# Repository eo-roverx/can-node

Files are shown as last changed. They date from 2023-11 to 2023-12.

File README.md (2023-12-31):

# CAN Node PCB Designs

Part of the new arm system, wherein each PCB drives one motor, provides it feedback control, and (if needed) gives back IMU and encoder data. Our CAN node will have the following features:

- CAN bus communication
- IMU (accelerometer, gyroscope)
- Motor encoder input
- Motor driver
- 4 user defined LEDs + one status LED
- 4 bit address DIP switch
- ESP32 microcontroller: integration and feedback control

## Components
- ESP32 Microcontroller
- ESP32 power capacitor
- MPU9250 IMU
- MCP2551 CAN Transceiver
- 2x CAN RJ45 ports
- 2x XT60 solder pads for power
- MD13 Motor Driver
- MD13 power XT60 solder pads
- MD13 signal JST
- motor encoder JST
- 5V buck converter
- 2x 4.7k ohms I2C pull-up resistors
- CAN termination resistor solder pads
- I2C debug solder pads
- CAN Rx-Tx debug solder pads
- 4x dip switch
- 4x 10k ohm pull-down resistors
- 1 power LED
- 1 status LED
- 4 user defined LEDs
    - 2 used for CRx-CTx
    - 1 used for MPU calibration
    - 1 used for sync
- 6x 2k ohm current limiting resistors

## ESP32 Pin-out

ESP32 Pin-out

### CAN Bus
-  D2 CAN Rx
- D15 CAN Tx

### IMU
- D21 SDA
- D22 SCL
- D18 FSYNC
- D19 INT

### Motor encoder
- D34 pin A
- D33 pin B

### MD13 Motor Driver
- D26 PWM
- D25 DIR

### LEDs
- D32 status
- D13 user 0 (Sync: all nodes are connected)
- D12 user 1 (CAN Rx)
- D14 user 2 (CAN Tx)
- D27 user 3 (MPU calibration)

### Address DIP switches
- D4 address 0
- RX2 address 1
- TX2 address 2
- D5 address 3

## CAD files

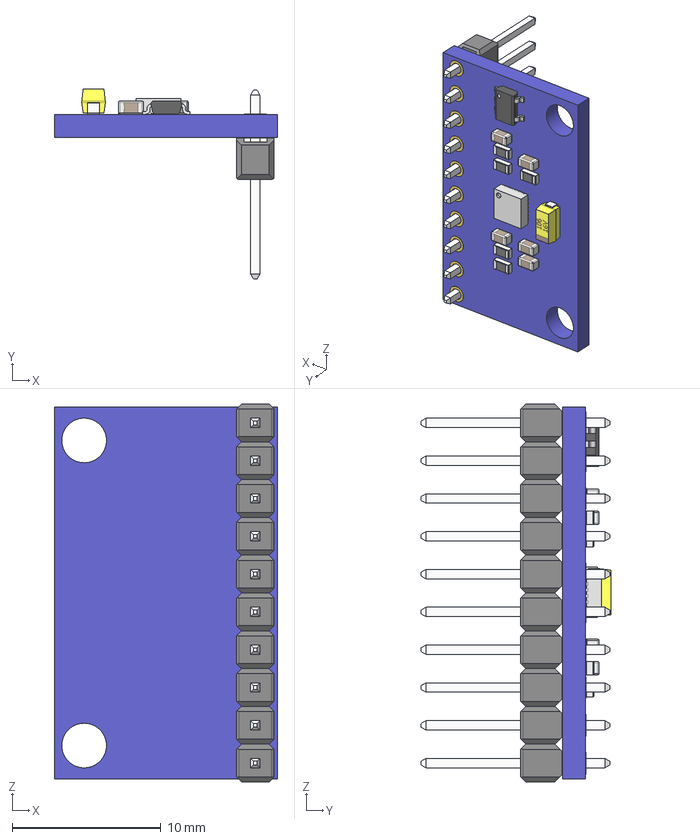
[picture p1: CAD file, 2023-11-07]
custom-libs/3d/MPU-9250.stp
15.0 x 12.8 x 25.4 mm
board
hole_plating x 20
Pin Header 1x10 TH Pitch 2.54mm
MPU-9250_1
tantalum 10uF
SOT23_5
RESC-0603 x 5
CAPC-0603-T0.9-BN x 5

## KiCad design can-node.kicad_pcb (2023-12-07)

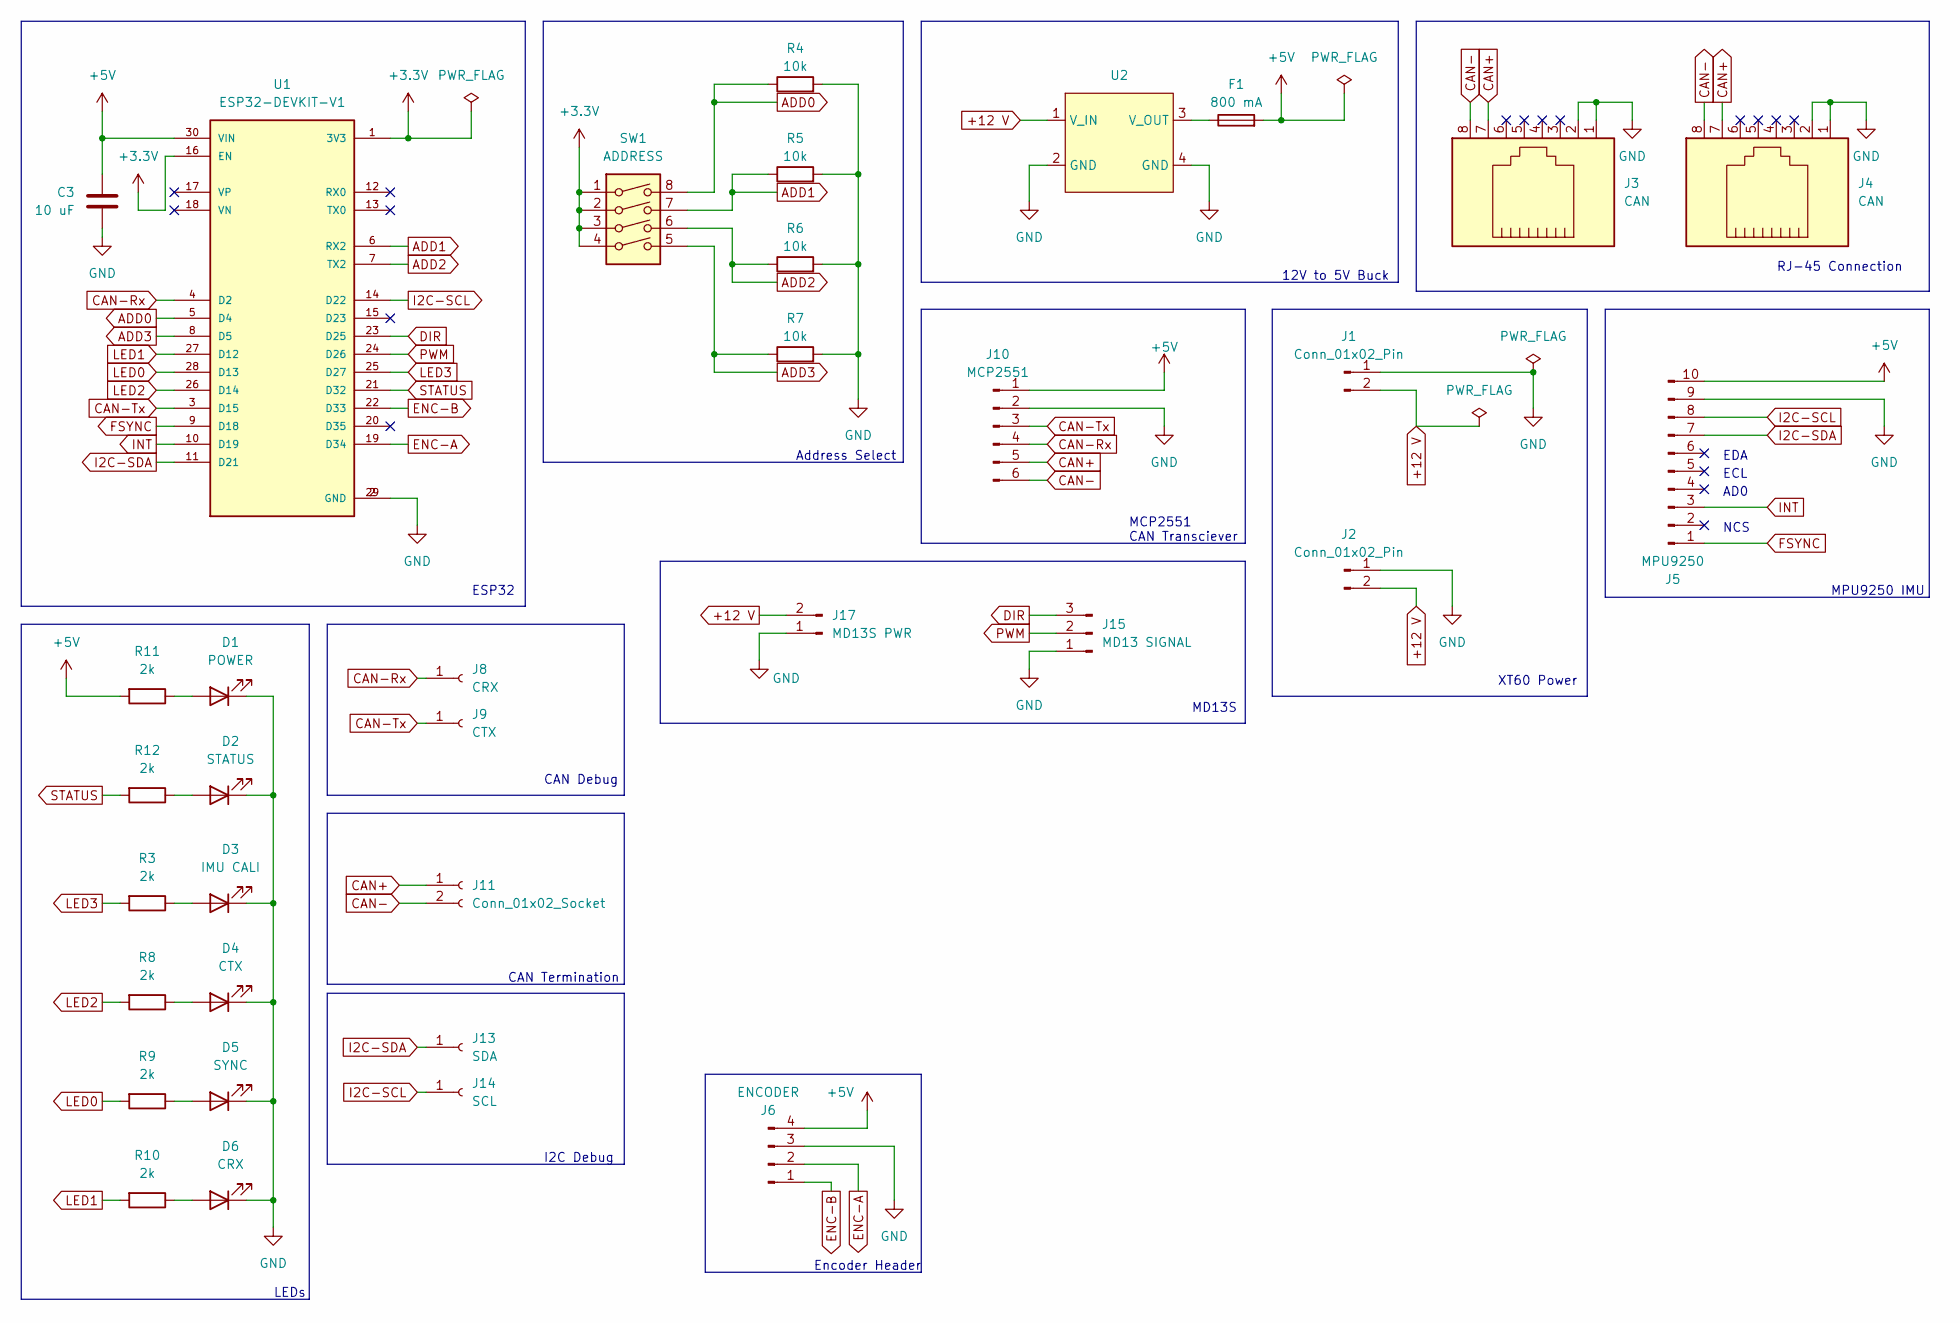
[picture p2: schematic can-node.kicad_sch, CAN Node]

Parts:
C3: 10 uF; C_0805_2012Metric
D1: POWER; LED_D3.0mm
D2: STATUS; LED_D3.0mm
D3: IMU CALI; LED_D3.0mm
D4: CTX; LED_D3.0mm
D5: SYNC; LED_D3.0mm
D6: CRX; LED_D3.0mm
F1: 800 mA; Fuse_0805_2012Metric_Pad1.15x1.40mm_HandSolder
J1, J2: Conn_01x02_Pin; SolderWire-1.5sqmm_1x02_P7.8mm_D1.7mm_OD3.9mm
J3, J4: CAN; RJ45_Amphenol_54602-x08_Horizontal
J5: MPU9250; PinHeader_1x10_P2.54mm_Vertical
J6: ENCODER; JST_PH_B4B-PH-K_1x04_P2.00mm_Vertical
J8: CRX; SolderWire-0.1sqmm_1x01_D0.4mm_OD1mm
J9: CTX; SolderWire-0.1sqmm_1x01_D0.4mm_OD1mm
J10: MCP2551; PinHeader_1x06_P2.54mm_Vertical
J11: Conn_01x02_Socket; SolderWire-0.1sqmm_1x02_P3.6mm_D0.4mm_OD1mm
J13: SDA; SolderWire-0.1sqmm_1x01_D0.4mm_OD1mm
J14: SCL; SolderWire-0.1sqmm_1x01_D0.4mm_OD1mm
J15: MD13 SIGNAL; JST_PH_S3B-PH-K_1x03_P2.00mm_Horizontal
J17: MD13S PWR; SolderWire-1sqmm_1x02_P7.8mm_D1.4mm_OD3.9mm
R3, R8, R9, R10, R11, R12: 2k; R_Axial_DIN0204_L3.6mm_D1.6mm_P5.08mm_Horizontal
R4, R5, R6, R7: 10k; R_Axial_DIN0204_L3.6mm_D1.6mm_P5.08mm_Horizontal
SW1: ADDRESS; SW_DIP_SPSTx04_Slide_6.7x11.72mm_W7.62mm_P2.54mm_LowProfile
U1: ESP32-DEVKIT-V1; MODULE_ESP32_DEVKIT_V1; PARTREV N/A
U2: MINI_360_Buck

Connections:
+3.3V: SW1.1, SW1.2, SW1.3, SW1.4, U1.1 (3V3), U1.16 (EN)
+5V: C3.1, F1.2, J5.10, J6.4, J10.1, R11.2, U1.30 (VIN)
+12 V: J1.2, J2.2, J17.2, U2.1 (V_IN)
ADD0: R4.1, SW1.8, U1.5 (D4)
ADD1: R5.1, SW1.7, U1.6 (RX2)
ADD2: R6.1, SW1.6, U1.7 (TX2)
ADD3: R7.1, SW1.5, U1.8 (D5)
CAN+: J3.7, J4.7, J10.5, J11.1
CAN-: J3.8, J4.8, J10.6, J11.2
CAN-Rx: J8.1, J10.4, U1.4 (D2)
CAN-Tx: J9.1, J10.3, U1.3 (D15)
DIR: J15.3, U1.23 (D25)
ENC-A: J6.2, U1.19 (D34)
ENC-B: J6.1, U1.22 (D33)
FSYNC: J5.1, U1.9 (D18)
GND: C3.2, D1.1 (K), D2.1 (K), D3.1 (K), D4.1 (K), D5.1 (K), D6.1 (K), J1.1, J2.1, J3.1, J3.2, J4.1, J4.2, J5.9, J6.3, J10.2, J15.1, J17.1, R4.2, R5.2, R6.2, R7.2, U1.2 (GND), U1.29 (GND), U2.2 (GND), U2.4 (GND)
I2C-SCL: J5.8, J14.1, U1.14 (D22)
I2C-SDA: J5.7, J13.1, U1.11 (D21)
INT: J5.3, U1.10 (D19)
LED0: R9.2, U1.28 (D13)
LED1: R10.2, U1.27 (D12)
LED2: R8.2, U1.26 (D14)
LED3: R3.2, U1.25 (D27)
unnamed: D1.2 (A), R11.1
unnamed: D2.2 (A), R12.1
unnamed: D3.2 (A), R3.1
unnamed: D4.2 (A), R8.1
unnamed: D5.2 (A), R9.1
unnamed: D6.2 (A), R10.1
unnamed: F1.1, U2.3 (V_OUT)
PWM: J15.2, U1.24 (D26)
STATUS: R12.2, U1.21 (D32)

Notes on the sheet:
ESP32
12V to 5V Buck
NCS
RJ-45 Connection
Address Select
MCP2551 CAN Transciever
CAN Termination
I2C Debug
ECL
XT60 Power
MPU9250 IMU
MD13S
LEDs
Encoder Header
AD0
CAN Debug
EDA

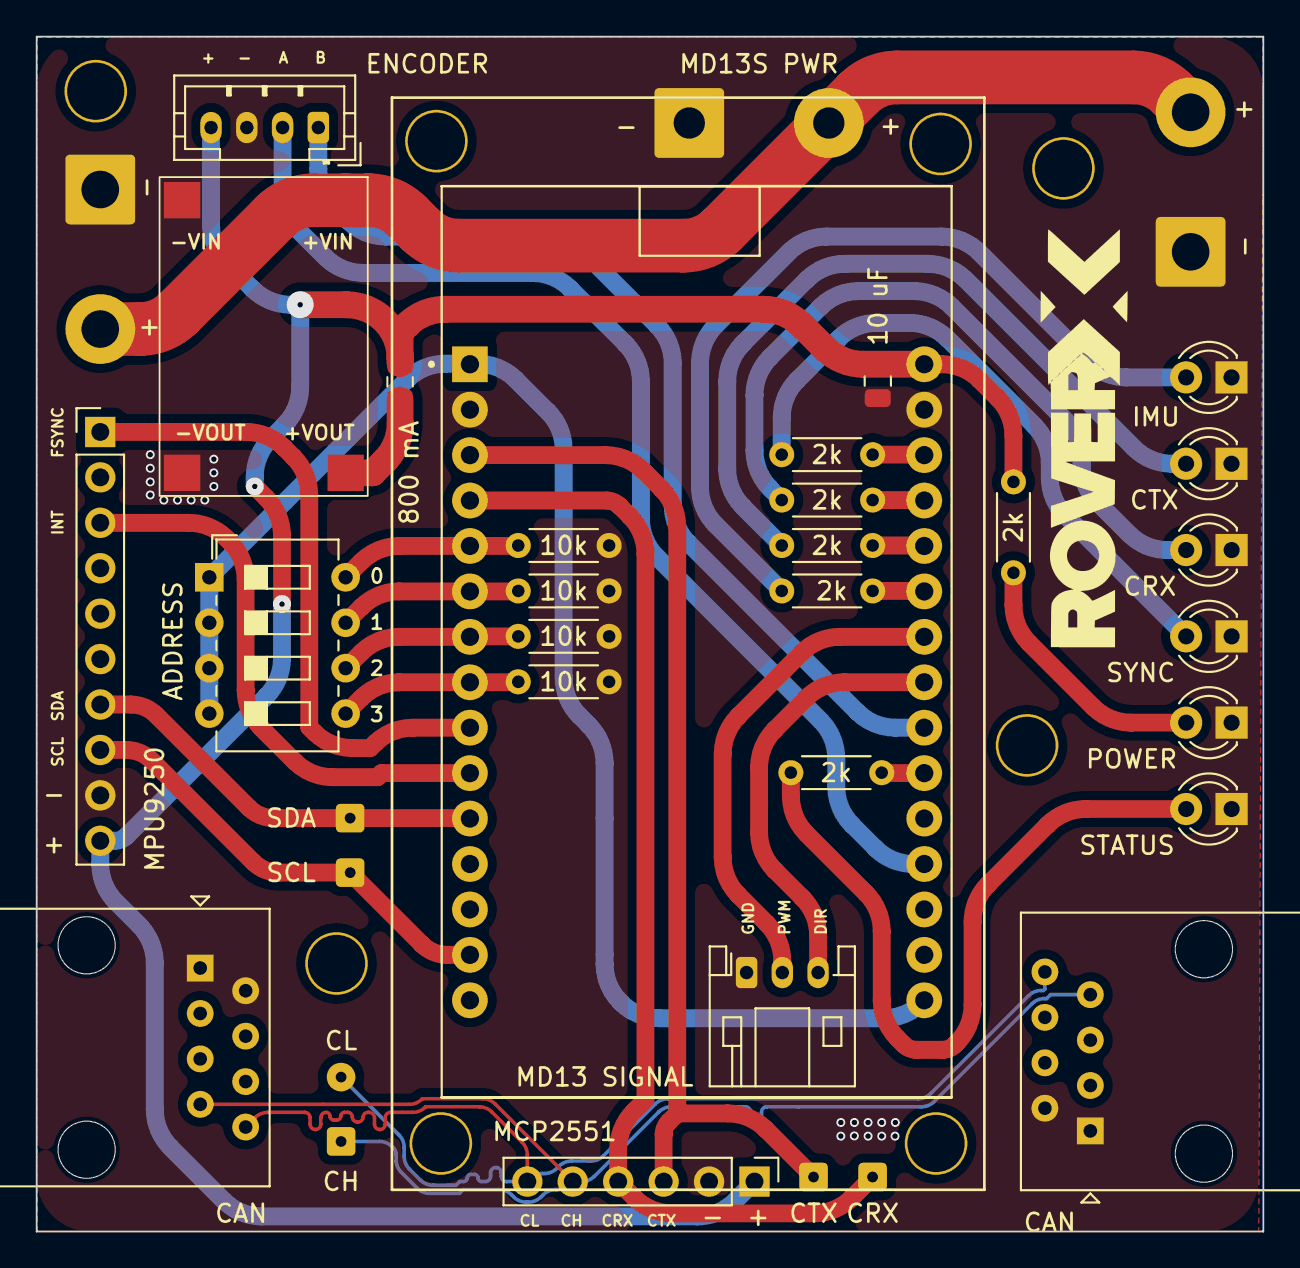
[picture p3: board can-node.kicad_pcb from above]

Board: 2 copper layers, 68.6 x 66.8 mm, 35 parts (0 on the bottom side), 32 nets.

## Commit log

2023-11-03 v1 for esp32 breakout
    [can-node.kicad_pcb, can-node.kicad_sch]
2023-11-04 placed PCB components
    [can-node.kicad_pcb, can-node.kicad_sch]
2023-11-04 additional labelling
    [can-node.kicad_pcb]
2023-11-06 first try
    [can-node.kicad_pcb, can-node.kicad_sch]
2023-11-07 fixed footprints
    [can-node.kicad_pcb, can-node.kicad_sch]
2023-11-07 routing attempt
    [can-node.kicad_pcb, can-node.kicad_sch]
2023-11-07 update for 3D
    [can-node.kicad_pcb, can-node.kicad_sch]
2023-11-09 update with feedback
    [can-node.kicad_pcb, can-node.kicad_sch]
2023-11-10 diff pair and mount holes
    [can-node.kicad_pcb]
2023-11-10 add vias
    [can-node.kicad_pcb]
2023-11-12 debug 5V trace
    [can-node.kicad_pcb]
2023-11-20 add silkscreen
    [can-node.kicad_pcb]
2023-11-24 add CAN Rx & CAN Tx LEDs
    [can-node.kicad_pcb]
2023-11-24 assign pins for other LEDs
2023-11-24 finish reroute
    [can-node.kicad_pcb, can-node.kicad_sch]
2023-11-24 smol silkscreen bug :)
    [can-node.kicad_pcb]
2023-11-25 silkscreen update
    [can-node.kicad_pcb]
2023-11-25 forgot small power components
2023-11-25 add esp32 usb to sk, ignore gerbers
    [can-node.kicad_pcb]
2023-11-28 fix 5V for MCP
    [can-node.kicad_pcb, can-node.kicad_sch]
2023-12-01 add 5V
    [can-node.kicad_pcb, can-node.kicad_sch]
2023-12-01 clean up silkscreen
    [can-node.kicad_pcb]
2023-12-07 rm i2c pull-ups
    [can-node.kicad_pcb, can-node.kicad_sch]
